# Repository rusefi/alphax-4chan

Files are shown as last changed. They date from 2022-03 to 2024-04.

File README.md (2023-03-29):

# AlphaX 4 channel

[buy at https://www.alphaxpr.com/](https://alphaxpr.com/product/4chan-neo/)

powerted by [rusEFI](https://github.com/rusefi/rusefi)

48 pin / 4 channel ECU

[User Documentation](https://github.com/rusefi/rusefi/wiki/AlphaX-4chan)

[Internal Documentation](https://docs.google.com/spreadsheets/d/1eW7kSP680lBT2MWl0ovFSy7t3at6WnlU7vX5ZDYfQZM)

Designed using [KiCAD 7](https://www.kicad.org/). Powered by [Hellen One](https://github.com/andreika-git/hellen-one) and [rusEFI](https://github.com/rusefi/rusefi)

Larger sibling of [alphax-2chan](https://github.com/rusefi/alphax-2chan)
Smaller sibling of [alphax-8chan](https://github.com/rusefi/alphax-8chan)

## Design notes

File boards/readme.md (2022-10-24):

4 layers

97 x 115 mm

1 Set 24 Pin FCI Ecu Oil To Gas Computer Board Connector Auto Housing Sealed Plug Socket 211PC249S8005 HCCPHPE24BKA90F

24Pin Auto FCI Oil To Gas Computer Board ECU Plug Electronic Connector Wiring Harness With 16/18AWG Cable

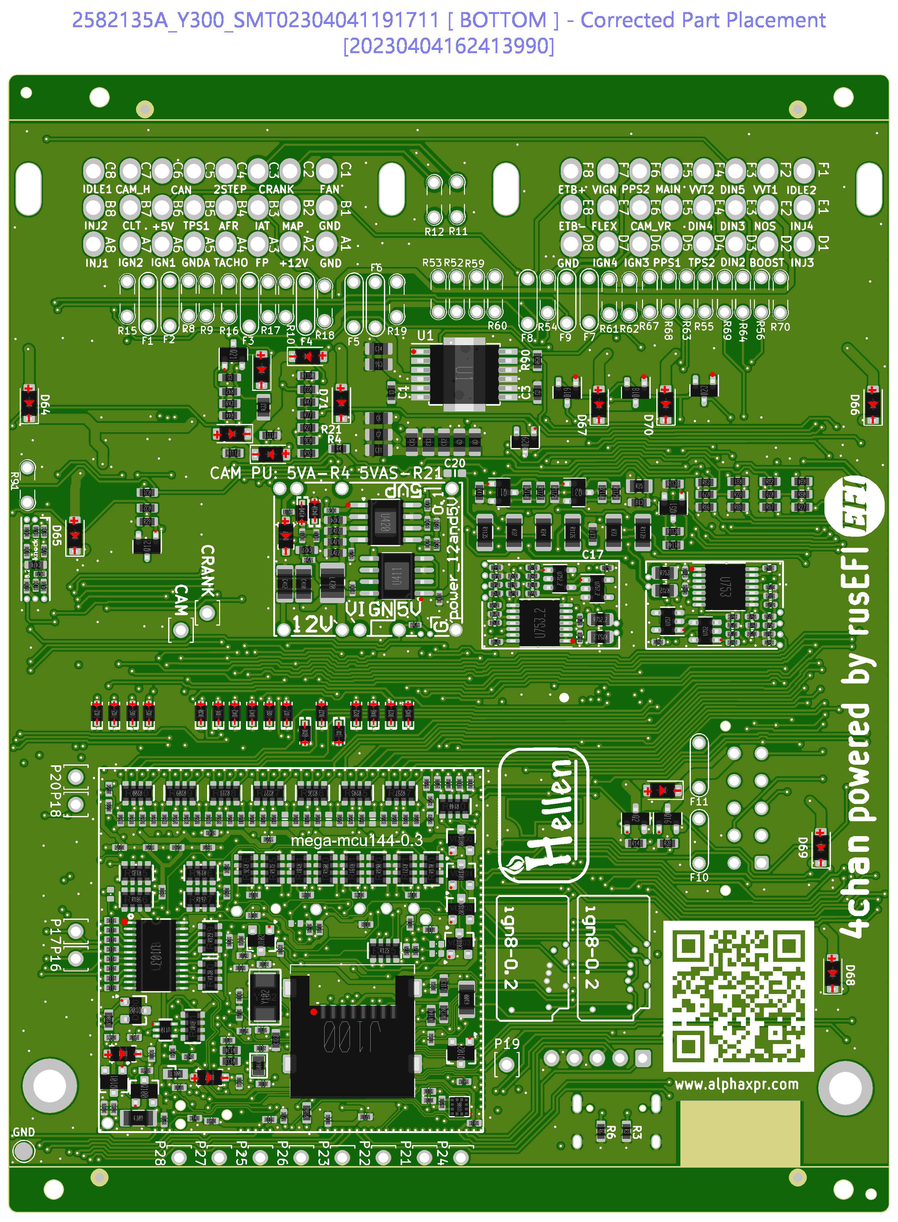
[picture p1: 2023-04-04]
boards/alphax_4ch-g/board/Produce_DanZhi.SMT_Snapshot.Bottom.2582135A_Y300.SMT02304041191711.png

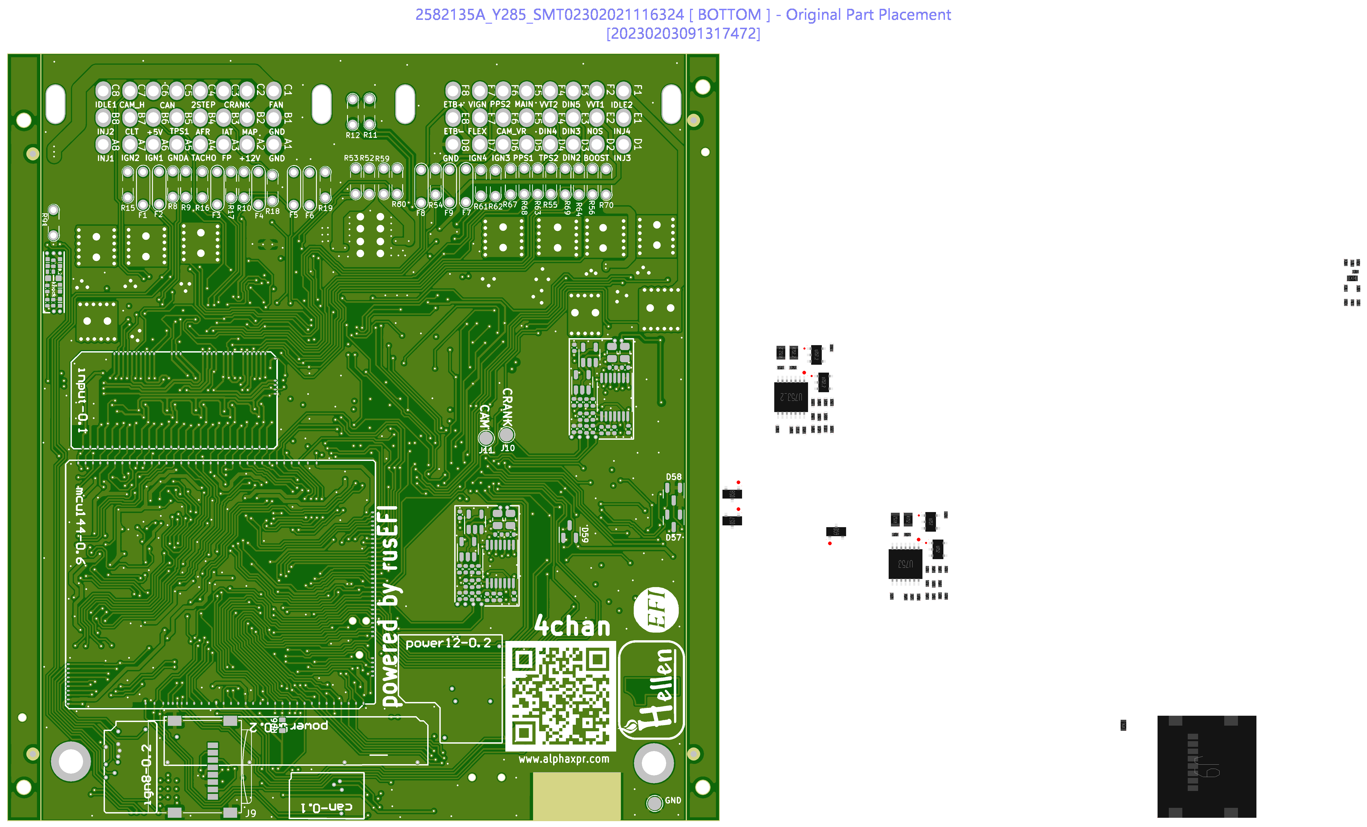
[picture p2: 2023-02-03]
boards/alphax_4ch-f.230202/board/Produce_DanZhi.SMT_Original_Snapshot.Bottom.2582135A_Y285.SMT02302021116324.png

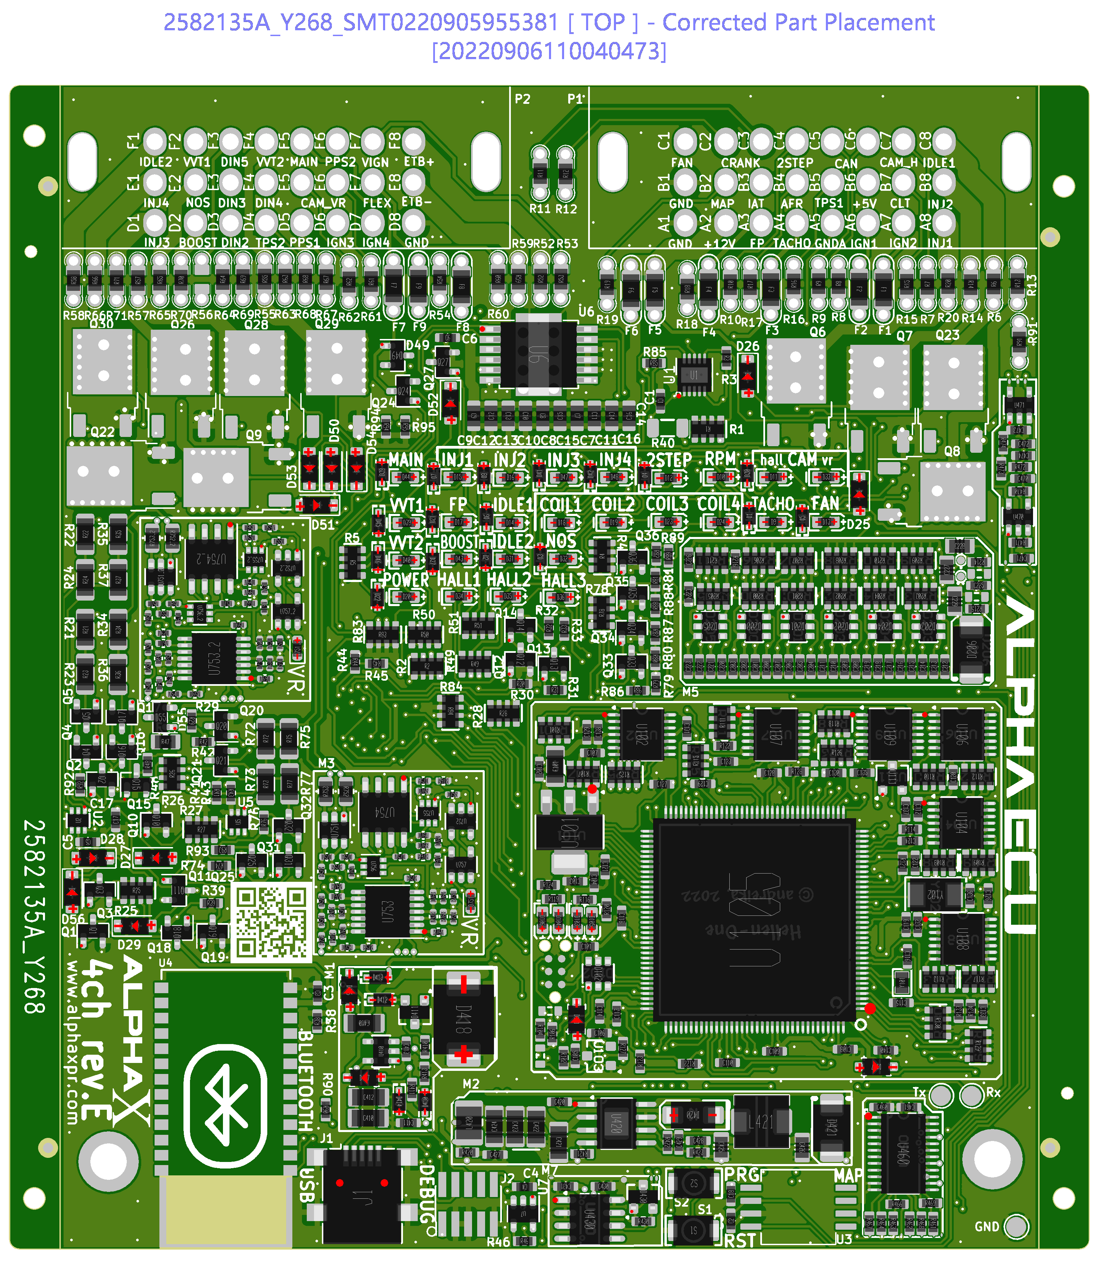
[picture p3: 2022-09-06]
boards/alphax_4ch-e.220905/board/Produce_DanZhi.SMT_Snapshot.Top.2582135A_Y268.SMT0220905955381.png

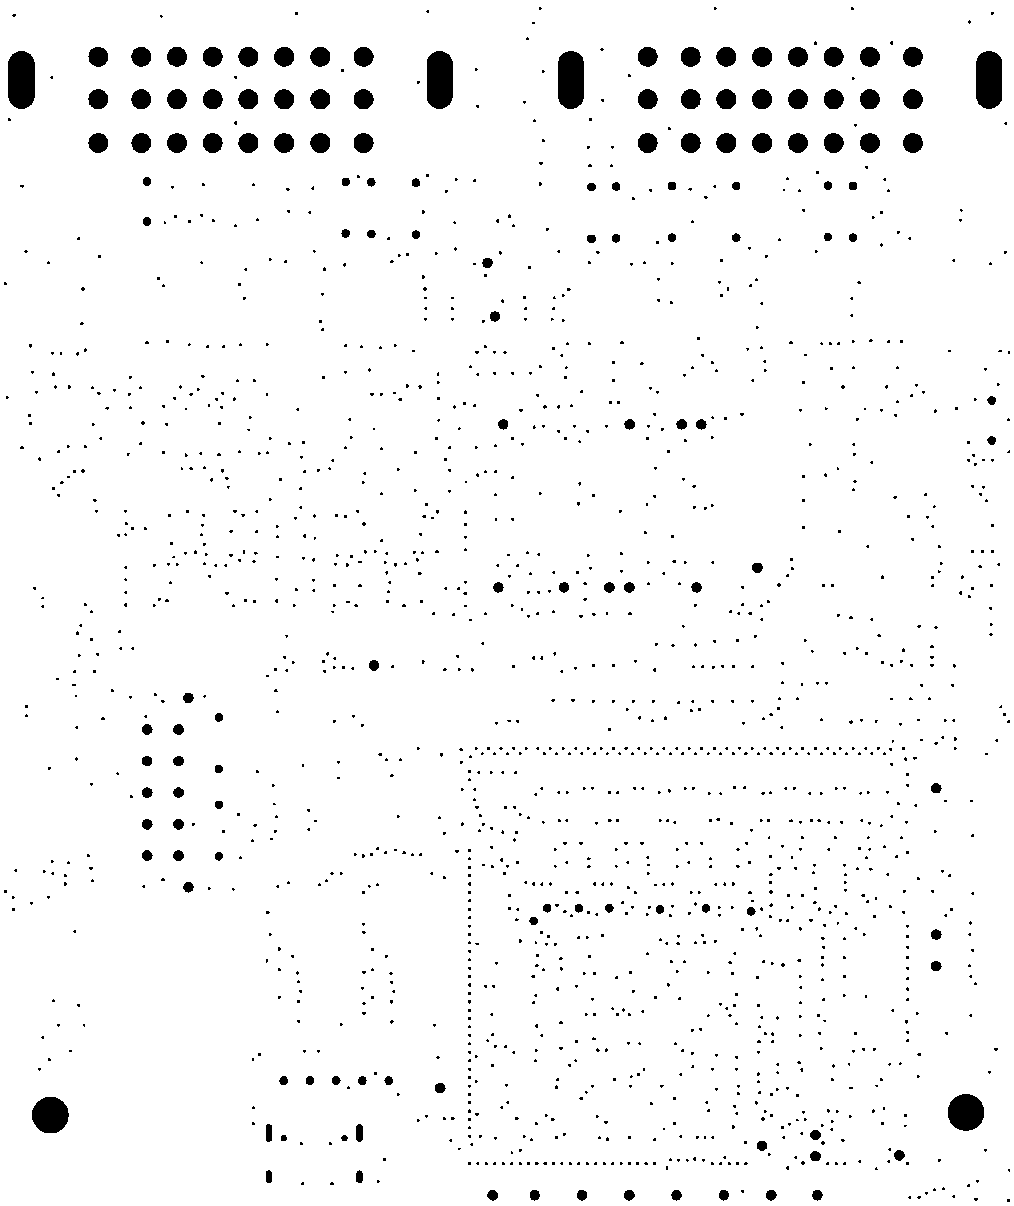
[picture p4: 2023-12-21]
boards/alphax_4ch-i/board/misc/alphax_4ch-i-outline.png

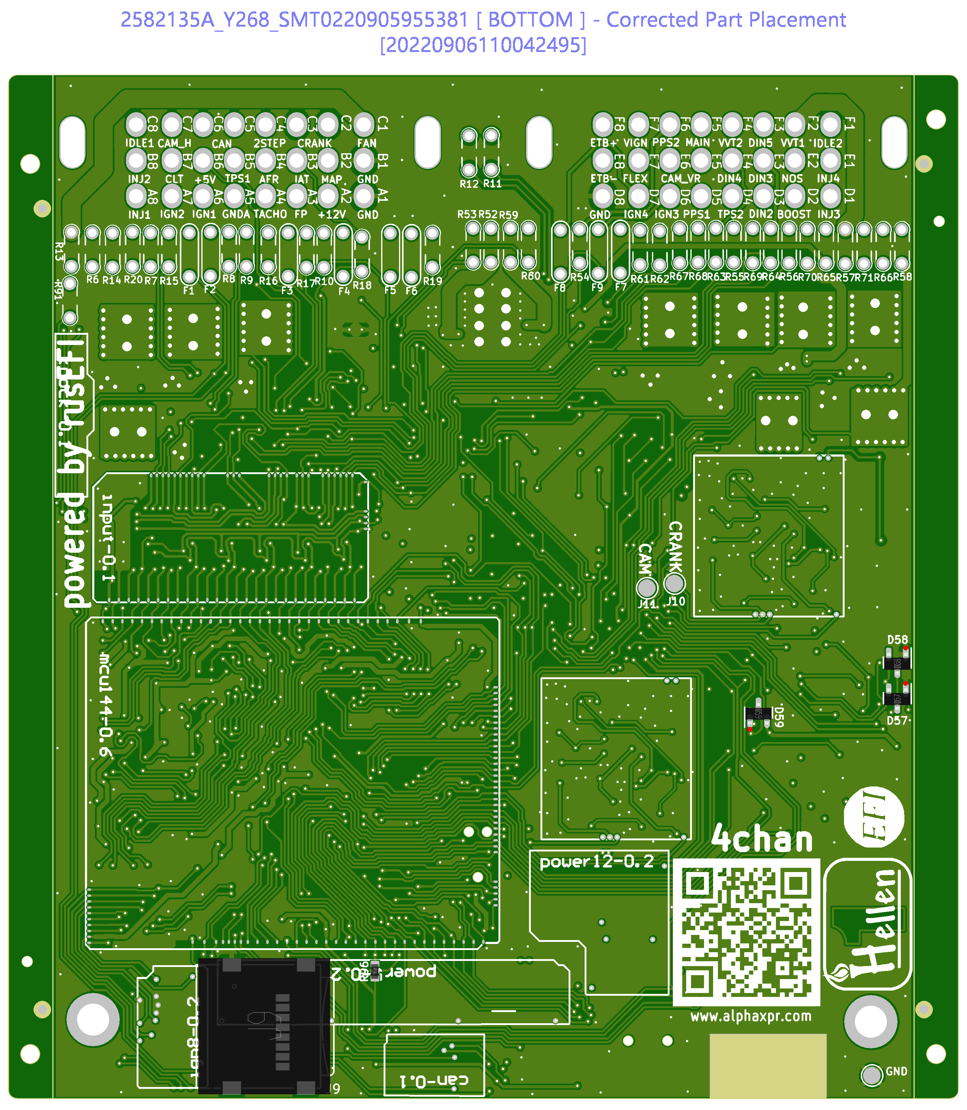
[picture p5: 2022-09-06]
boards/alphax_4ch-e.220905/board/Produce_DanZhi.SMT_Snapshot.Bottom.2582135A_Y268.SMT0220905955381.png

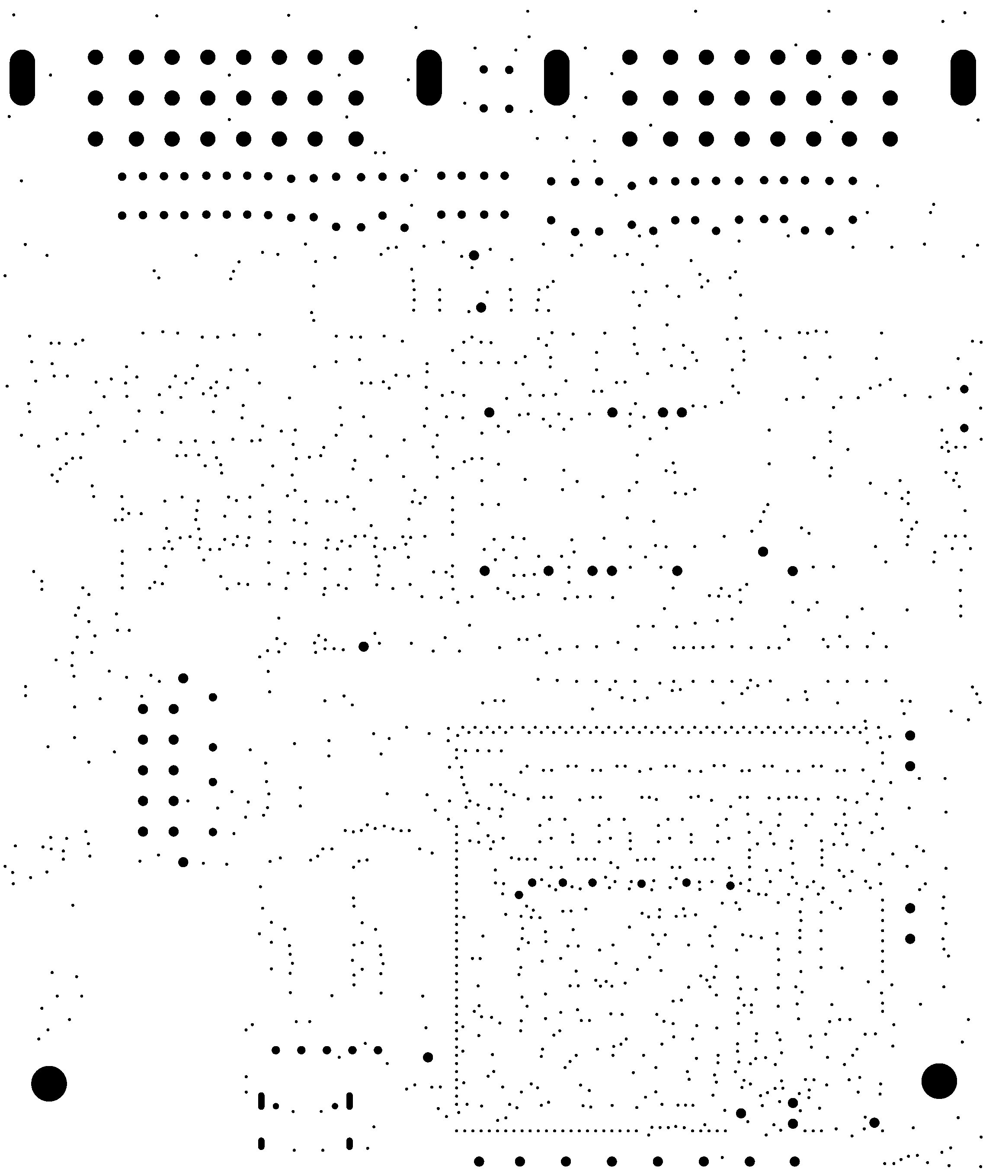
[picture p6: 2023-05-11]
boards/alphax_4ch-h.original/board/misc/alphax_4ch-h-outline.png

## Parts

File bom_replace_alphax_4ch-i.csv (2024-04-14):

############# MM SETUP ###############
# remove +5V pull-ups from SPI1, because we use it with +3.3v accelerometer
R103,
R105,
# remove jumper resistor connecting BOOT1 with A22 input line, because we use STM32F4
R131,
#CAN WAKEUP (disable O2S input)
R143,
############# MM SETUP ###############
# 4chan now prefers F42x for extra RAM
#U105,"STM32F427","LQFP144","C117816"
# F7 is even better than F42x!
U105,"STM32F767","LQFP144","C91685"
# DC-DC Inductor
L421,"MWSA0503S-100MT","MWSA0503","C408412"
L420,"NLCV32T-2R2M-EF","L1210","C250227"
# smart MOSFETs
"Q6,Q7,Q26,Q30,Q41,Q42,Q43,Q44,Q45,Q46,Q47,Q48","VND14NV04TR-E","DPAK","C2649436"
#MAX9142
"U754,U754_2","TLV3202AIDR","SO8","C129325"
#SD Card
J100,"TF-014-H16","SMD","C2874208"
# fuses
F410,"nSMD050-24V","SMD1206","C70076"
"F5,F6","Fuse-5A-1206","SMD1206","C553924"
"F1,F2,F8,F9,F10,F11","nSMD005","PAD-1206-PAD","C70064"
# TLS115
U411,"TLS115B0EJXUMA1","PG-DSO-8","C3743696"
# JLC shortage
R49,"4D03WGF1001T5E","R0603-4","C425239"
#20MHz crystal
Y102,"TXM20M0002503LFBEO00T","SMD5032-2P","C362485"
#WakeUP buffer
U110,"74LVC1G06SE-7","SOT-353","C460519"
#Blue LEDs
"D105,D109,D110,D111,D112,D113,D114,D115,D116","HL-PST-1608H203BC","LED0603","C497940"
#Green LEDs
"D20,D751,D104,D108,D751_2","XL-1608UGC-04","LED0603","C965804"
# remove R40 because we'll populate TLS115
R40,
#board ID capacitor shortage
C133,"1u","C0603","C519559"
# no software for accelerometer
U106,
#aux connector
J6,"430451012","02x05","C277725"
#mux
"U755,U756,U270,U275,U280,U285,U755_2,U756_2","WAS3157B-6","SOT-363","C213161"
# no Cortex 5x2 header
J2,"Cortex_Debug","PinHeader_2x05_P1.27mm_Vertical_SMD",""
# with MAP sensor
U3,"MPXH6400A","MPXH6400A-SSOP8","C511770"
# shortage
"R49","4D03WGF1001T5E","R0603-4","C110021"
#D1-D4 0 series
R140,"0","R0603x4","C1952"
# black main connector
P1,"HCCPHPE24BKA90F","33311-24AW-2","C5349068"
#include hellen-one/board_id/generated/board_id_alpha4ch-i.csv
#include bom_pullups_alphax_4ch-i.csv

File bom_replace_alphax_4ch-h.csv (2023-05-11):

############# MM SETUP ###############
# remove +5V pull-ups from SPI1, because we use it with +3.3v accelerometer
R103,
R105,
# remove jumper resistor connecting BOOT1 with A22 input line, because we use STM32F4
R131,
#CAN WAKEUP (disable O2S input)
R143,
############# MM SETUP ###############
# 4chan now prefers F42x for extra RAM
U105,"STM32F427","LQFP144","C117816"
# DC-DC Inductor
L421,"MWSA0503S-100MT","MWSA0503","C408412"
# smart MOSFETs
"Q6,Q7,Q26,Q30,Q41,Q42,Q43,Q44,Q45,Q46,Q47,Q48","VND10N06TR-E","DPAK","C2149912"
#SD Card
J100,"TF-014-H16","SMD","C2874208"
# fuses
F410,"nSMD050-24V","SMD1206","C70076"
"F5,F6","Fuse-5A-1206","SMD1206","C553924"
"F1,F2,F8,F9,F10,F11","nSMD005","PAD-1206-PAD","C70064"
# TLS115
U411,"TLS115B0EJXUMA1","PG-DSO-8","C3743696"
# JLC shortage
R49,"4D03WGF1001T5E","R0603-4","C425239"
#20MHz crystal
Y102,"TXM20M0002503LFBEO00T","SMD5032-2P","C362485"
#SMCJ30A
D418,"SMCJ30A","SMC","C320561"
#WakeUP buffer
U110,"74LVC1G06SE-7","SOT-353","C460519"
# remove R40 because we'll populate TLS115
R40,
# no software for accelerometer
U1001,
# no Cortex 5x2 header
J2,"Cortex_Debug","PinHeader_2x05_P1.27mm_Vertical_SMD",""
# no MAP sensor
U3,"MPXH6400A","MPXH6400A-SSOP8",""
#D1-D4 0 series
R140,"0","R0603x4","C1952"
#include hellen-one/board_id/generated/board_id_alpha4ch-h.csv
#include bom_pullups_alphax_4ch-h.csv

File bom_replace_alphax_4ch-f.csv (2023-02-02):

# remove the jumper connection from VCC_PP1 to +5V: we need +12v power supply for push-pull outputs.
R309
# remove +5V pull-ups from SPI1 | because we use it with +3.3v accelerometer
R103
R105
# remove jumper resistor connecting BOOT1 with A22 input line | because we use STM32F4
R131
# STM32
U105 | STM32F407ZGT6 | LQFP144 | C19156
#Alpha4Ch: We don't use VREF1 & VREF2 | so we don't need these resistors
R212
R213
# DC-DC Inductor
L421 | MWSA0503S-100MT | MWSA0503 | C408412
L420 | LBC3225T2R2MR | L1210 | C223413
# LMR14020->LMR14030 (more power | no problem)
U420 | LMR14030 | SOP8 | C182078
#fuses
F101 | nSMD035-16V | SMD1206 | C70072
F410 | nSMD050-24V | SMD1206 | C70076
F300 | nSMD050-24V | SMD1206 | C70076
F5 | Fuse-5A-1206 | SMD1206 | C553924
F6 | Fuse-5A-1206 | SMD1206 | C553924
#power distribution
U103 | AP2331W-7 | SOT-23 | C460346
U480 | AP2331W-7 | SOT-23 | C460346
# JLC-BOM stock shortages...
U420 | LMR14020SDDAR | SOP8 | C187824
S1 | TS-1088R-02026 | SMD-2_2.9x3.9x1.7 | C455280
S2 | TS-1088R-02026 | SMD-2_2.9x3.9x1.7 | C455280
L420 | NLV32T-2R2J-PF | L1210 | C89016
R4,R49 | 4D03WGF1001T5E | R0603-4 | C425239
# trigger schmidt buffer
U2,U5 | 74LVC2G17GW | SOT-363 | C80500
# analog switches for VR-discrete
U755, U756, U755_2, U756_2 | WAS3157B-6 | SOT-363 | C213161
U754, U754_2 | TLV3202AIDR | SO8 | C129325
# smart MOSFETs
Q6 | VND10N06TR-E | DPAK | C2149912
Q7 | VND10N06TR-E | DPAK | C2149912
Q8 | VND10N06TR-E | DPAK | C2149912
Q9 | VND10N06TR-E | DPAK | C2149912
Q22 | VND10N06TR-E | DPAK | C2149912
Q23 | VND10N06TR-E | DPAK | C2149912
Q26 | VND10N06TR-E | DPAK | C2149912
Q28 | VND10N06TR-E | DPAK | C2149912
Q29 | VND10N06TR-E | DPAK | C2149912
Q30 | VND10N06TR-E | DPAK | C2149912
# no TLE9201SG
U6 | IFX9201SG | Infineon_PG-DSO-12-11 | C112633
# use cheaper components
Q1, Q2, Q10, Q11, Q12, Q15, Q19, Q20, Q21, Q24, Q25, Q27, Q33, Q34, Q35, Q36 | AO3400A | SOT-23 | C700953
Q3, Q4, Q5, Q13, Q14, Q16, Q17, Q18, Q31, Q32 | AO3401A | SOT-23 | C700954
#
U752, U757, U752_2, U757_2 | 74AHC1G02 | SOT23-5 | C163710
F1, F2, F8, F9 | nSMD005 | PAD-1206-PAD | C70064
#a bit optional
U103
# remove R40 because we'll populate TLS115
R40
# no Cortex 5x2 header
J2 | Cortex_Debug | PinHeader_2x05_P1.27mm_Vertical_SMD
# no MAP sensor
U3 | MPXH6400A | MPXH6400A-SSOP8
#include hellen-one/board_id/generated/board_id_alpha4ch-f.csv

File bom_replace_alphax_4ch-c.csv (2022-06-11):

# remove the jumper connection from VCC_PP1 to +5V: we need +12v power supply for push-pull outputs.
R309
# remove +5V pull-ups from SPI1 | because we use it with +3.3v accelerometer
R103
R105
# remove jumper resistor connecting BOOT1 with A22 input line | because we use STM32F4
R131
# STM32
U105 | STM32F407ZGT6 | LQFP144 | C19156
#Alpha4Ch: We don't use VREF1 & VREF2 | so we don't need these resistors
R212
R213
# DC-DC Inductor
L421 | MWSA0503S-100MT | MWSA0503 | C408412
L420 | LBC3225T2R2MR | L1210 | C223413
# LMR14020->LMR14030 (more power | no problem)
U420 | LMR14030 | SOP8 | C182078
#fuses
F101 | nSMD035-16V | SMD1206 | C70072
F410 | nSMD050-24V | SMD1206 | C70076
F300 | nSMD050-24V | SMD1206 | C70076
F5 | Fuse-5A-1206 | SMD1206 | C553924
F6 | Fuse-5A-1206 | SMD1206 | C553924
#power distribution
U103 | AP2331W-7 | SOT-23 | C460346
U480 | AP2331W-7 | SOT-23 | C460346
# JLC-BOM stock shortages...
U420 | LMR14020SDDAR | SOP8 | C187824
S1 | TS-1088R-02026 | SMD-2_2.9x3.9x1.7 | C455280
S2 | TS-1088R-02026 | SMD-2_2.9x3.9x1.7 | C455280
L420 | NLV32T-2R2J-PF | L1210 | C89016
R4 | 4D03WGF1001T5E | R0603-4 | C425239
# trigger schmidt buffer
U2 | 74HC2G17GW | SOT-363 | C94189
U5 | 74HC2G17GW | SOT-363 | C94189
# analog switches for VR-discrete
U755, U756, U755_2, U756_2 | WAS3157B-6 | SOT-363 | C213161
# smart MOSFETs
Q6 | VND14NV04TR-E | DPAK | C2649436
Q7 | VND14NV04TR-E | DPAK | C2649436
Q8 | VND14NV04TR-E | DPAK | C2649436
Q9 | VND14NV04TR-E | DPAK | C2649436
Q22 | VND14NV04TR-E | DPAK | C2649436
Q23 | VND14NV04TR-E | DPAK | C2649436
Q26 | VND14NV04TR-E | DPAK | C2649436
Q28 | VND14NV04TR-E | DPAK | C2649436
Q29 | VND14NV04TR-E | DPAK | C2649436
Q30 | VND14NV04TR-E | DPAK | C2649436
# use cheaper components
Q1, Q2, Q10, Q11, Q12, Q15, Q19, Q20, Q21, Q24, Q25, Q27, Q33, Q34, Q35, Q36 | AO3400A | SOT-23 | C700953
Q3, Q4, Q5, Q13, Q14, Q16, Q17, Q18, Q31, Q32 | AO3401A | SOT-23 | C700954
# remove R40 because we'll populate TLS115
R40
# no TLS115
U1 | TLS115 | PG-DSO-8-43
# no Cortex 5x2 header
J2 | Cortex_Debug | PinHeader_2x05_P1.27mm_Vertical_SMD
# no MAP sensor
U3 | MPXH6400A | MPXH6400A-SSOP8
# no TLE9201SG
U6 | TLE9201SG | Infineon_PG-DSO-12-11
#include board_id_alpha4ch-c.csv

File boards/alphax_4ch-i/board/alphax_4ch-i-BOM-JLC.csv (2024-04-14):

Comment | Designator | Footprint | LCSC Part #
10n | C1, C3 | C0603 | C57112
100n | C2, C5, C6, C18, C19, C55, C460, C461, C460_2, C461_2 | C0603 | C14663
1n | C4 | C0603 | C1588
22u | C7, C117, C123 | C0603 | C59461
1n 250V | C8, C9, C17, C20, C21 | C0603 | C277510
10u | C45, C46, C47, C48, C49, C50, C51, C52, C53, C54 | C0805 | C15850
1N4148WS | D1, D2, D3, D5, D6, D7, D8, D21, D22, D24, D37, D38, D41, D42, D45, D46, D53, D410, D412, D413, D414 | SOD-323 | C2128
LED-WHITE-0603 | D4, D10, D33, D34, D35, D36 | LED-0603 | C2290
LED-RED-0603 | D9, D13, D14, D15, D16, D17, D31, D32, D39, D40, D43, D44, D47, D48, D56, D57, D103 | LED-0603 | C2286
BAT54S | D18, D19, D23, D55, D58, VD100, VD101, VD102, VD103 | SOT-23 | C47546
PSM712-LF | D25, D28, D29, D411 | SOT-23 | C32677
B5819W | D26, D27, D49, D50, D51, D52, D64, D65, D66, D67, D68, D69, D70, D71, D72, D416, D417, D101, D107 | SOD-123 | C8598
nSMD050 | F3, F4, F7 | PAD-1206-PAD | C720075
USB_C_Receptacle_USB2.0 | J1 | USB_C_Receptacle_XKB_U262-16XN-4BVC11 | C2927038
AO3400A | Q1, Q3, Q4, Q8, Q9, Q10, Q11, Q12, Q17, Q20, Q22, Q23, Q24, Q27, Q29, Q31, Q51, Q101, Q103 | SOT-23 | C20917
PJM2319PSA | Q2, Q16 | SOT-23 | C411720
AO3401A | Q13, Q14, Q18, Q19, Q21, Q25, Q28, Q35, Q36, Q49, Q50, Q52, Q53, Q100, Q102 | SOT-23 | C15127
4.7k | R1, R2, R5, R26, R50, R51, R125, R170, R171, R175, R176, R180, R181, R185, R186, R190, R191, R196, R197, R200, R209, R218, R227, R236, R245, R257 | R0603-4 | C66697
5.6k | R3, R6 | R0603 | C23189
2k | R4, R18, R19, R34, R1126, R1131, R1135, R1136, R1139, R1141 | R1206 | C17944
4.7k | R7, R8, R14, R20, R27, R29, R30, R38, R39, R41, R42, R43, R44, R52, R53, R54, R55, R57, R86, R87, R88, R98, R99, R1100, R1101, R1102, R1103, R1104, R1105, R1106, R1107, R1108, R1109, R1110, R1111, R1112, R1113, R1125, R1127, R1128, R1129, R1132, R1137, R1138, R1140 | R0603 | C23162
4.7k | R9, R10, R11, R12, R21, R22, R23, R24, R35, R36, R37, R47, R72, R73 | R1206 | C17936
10k | R16 | R0603 | C25804
33k | R17, R120 | R0603 | C4216
470 | R25 | R0805 | C17710
1.2k | R28, R78, R79, R80 | R0603 | C22765
2.7k | R31, R32 | R0603 | C13167
220 | R33 | R0805 | C17557
SMD1206B035TF/16 | F100, F101 | R1206 | C269114
750 | R45 | R0805 | C17818
680k | R46, R74, R76, R93 | R0603 | C25822
Jumper-Pad-Pad | R56, R91 | PAD-0805-PAD | C17477
6.8k | R58 | R0603 | C23212
3.3k | R81, R82, R83, R84, R85 | R0603 | C22978
MAX9924UAUB+ | U1 | MSOP-10_3x3mm_P0.5mm | C143633
TLE9201SG | U7 | Infineon_PG-DSO-12-11 | C112633
47u | C410, C412 | C1206 | C96123
100n | C411, C413, C420, C470, C203, C202, C207, C206, C205, C204, C217, C218, C225, C226 | C0402 | C307331
1u | C414, C415, C755, C758, C761, C762, C763, C765, C766, C767, C755_2, C758_2, C761_2, C762_2, C763_2, C765_2, C766_2, C767_2 | C0402 | C52923
10u | C421, C422, C423, C424, C425, C426 | C0603 | C96446
4.7u | C427 | C0603 | C19666
10n | C428, C756, C757, C760, C764, C768, C769, C756_2, C757_2, C760_2, C764_2, C768_2, C769_2, C213, C214 | C0402 | C15195
220p | C429 | C0402 | C1530
SMCJ30A | D418 | SMC | C310046
SS34 | D420 | SMA | C8678
P6SMB6.8CA | D421, D205 | SMB | C78395
MHT136UGCT | LED1, LED2, LED3, LED4 | LED0402 | C434447
6.8k | R410, R413 | R0402 | C25917
33k | R411, R424, R425, R474 | R0402 | C25779
1 | R420 | R0402 | C25086
10k | R421, R426, R427, R757, R762, R763, R767, R768, R102, R107, R108, R109, R121, R127, R128, R141, R142, R757_2, R762_2, R763_2, R767_2, R768_2, R233, R234 | R0402 | C25744
68k | R422, R760, R760_2 | R0402 | C36871
12k | R423, R754, R754_2, R472 | R0402 | C25752
4.7k | R428, R144, R210 | R0402 | C25900
MIC5205-3.3YM5 | U410 | SOT23-5 | C37970
LMR14020 | U420 | SOP8 | C187824
10 | R461, R462, R463, R464, R466, R467, R468, R469, R461_2, R462_2, R463_2, R464_2, R466_2, R467_2, R468_2, R469_2 | R0603 | C22859
SN74LVC4245APWR | U460, U103, U460_2 | TSSOP24 | C7859
1n | C751, C135, C139, C141, C142, C751_2, C211, C209, C208, C201, C200, C216, C219, C215, C212, C227, C230, C231, C232, C233, C210, C143, C144, C145, C146 | C0402 | C1523
470n | C752, C752_2 | C0402 | C47339
100n | C753, C754, C759, C100, C101, C105, C108, C109, C110, C111, C112, C113, C118, C119, C120, C121, C122, C124, C126, C127, C128, C129, C130, C134, C147, C170, C175, C180, C185, C190, C195, C220, C221, C222, C270, C275, C280, C285, C753_2, C754_2, C759_2 | C0402 | C1525
2.2k | R751, R122, R123, R146, R147, R751_2 | R0402 | C25879
10k | R752, R753, R752_2, R753_2 | R0805 | C17414
100k | R755, R756, R758, R759, R755_2, R756_2, R758_2, R759_2, R471, R473 | R0402 | C25741
10 | R761, R764, R769, R110, R111, R112, R113, R114, R115, R116, R117, R761_2, R764_2, R769_2 | R0402 | C25077
1k | R765, R766, R765_2, R766_2 | R0402 | C11702
SRV05-4-P-T7 | U751, D102, D200, D201, D202, D203, D204, D206, D207, U751_2 | SOT23-6 | C85364
74AHC1G02 | U752, U757, U752_2, U757_2 | SOT23-5 | C7463
MCP6004 | U753, U170, U175, U180, U185, U190, U195, U753_2 | TSSOP14 | C50282
TJA1051T/3/1J | U100 | SO8 | C38695
REF3033 | U102 | SOT-23 | C36658
PESD1CAN | D100 | SOT-23 | C343993
LPS22HBTR | U107 | HLGA-10L | C94049
LED-YELLOW-0603 | D106 | LED-0603 | C72038
LDL1117S33R | U101 | SOT-223 | C435835
BTN | S100, S101 | SMD-2_2.9x3.9x1.7 | C115357
BLM18AG601SN1D | L100 | L0603 | C19330
680k | R222, R208, R207, R242, R243, R237, R250, R251, R225 | R0402 | C163456
510 | R254, R255, R256, R258 | R0402 | C25123
470 | R101, R118, R119 | R0603-4 | C25510
120 | R100 | R0603 | C22787
100 | R104, R106 | R0603 | C22775
74LVC2G17GW,125 | U108, U109 | SOT-363 | C80500
32.768 kHz | Y101 | SMD2012 | C99009
18p | C132, C136 | C0402 | C1549
12p | C115, C116 | C0402 | C1547
10k | R129, R130 | R0603-4 | C29718
5.1k | R195 | R0402 | C25905
4.7u | C102, C103, C104, C106, C107, C137, C138, C140 | C0402 | C23733
2.2u | C114, C131, C223, C224, C229 | C0402 | C12530
0 | R145 | R0402 | C17168
3.3n | C471 | C0402 | C26404
330p | C472 | C0402 | C13533
47p | C473 | C0402 | C1567
680p | C474 | C0603 | C1630
470k | R470 | R0402 | C25790
LMV321IDBVR | U470, U471 | SOT23-5 | C7972
STM32F767 | U105 | LQFP144 | C91685
MWSA0503S-100MT | L421 | MWSA0503 | C408412
NLCV32T-2R2M-EF | L420 | L1210 | C250227
VND14NV04TR-E | Q6, Q7, Q26, Q30, Q41, Q42, Q43, Q44, Q45, Q46, Q47, Q48 | DPAK | C2649436
TLV3202AIDR | U754, U754_2 | SO8 | C129325
TF-014-H16 | J100 | SMD | C2874208
nSMD050-24V | F410 | SMD1206 | C70076
Fuse-5A-1206 | F5, F6 | SMD1206 | C553924
nSMD005 | F1, F2, F8, F9, F10, F11 | PAD-1206-PAD | C70064
TLS115B0EJXUMA1 | U411 | PG-DSO-8 | C3743696
TXM20M0002503LFBEO00T | Y102 | SMD5032-2P | C362485
74LVC1G06SE-7 | U110 | SOT-353 | C460519
HL-PST-1608H203BC | D105, D109, D110, D111, D112, D113, D114, D115, D116 | LED0603 | C497940
XL-1608UGC-04 | D20, D751, D104, D108, D751_2 | LED0603 | C965804
1u | C133 | C0603 | C519559
430451012 | J6 | 02x05 | C277725
WAS3157B-6 | U755, U756, U270, U275, U280, U285, U755_2, U756_2 | SOT-363 | C213161
MPXH6400A | U3 | MPXH6400A-SSOP8 | C511770
4D03WGF1001T5E | R49 | R0603-4 | C110021
0 | R140 | R0603x4 | C1952
HCCPHPE24BKA90F | P1 | 33311-24AW-2 | C5349068
750 | R133 | R0603 | C23241
1500 | R134 | R0603 | C22843

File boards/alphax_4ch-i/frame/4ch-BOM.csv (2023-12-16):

Comment | Designator | Footprint | LCSC Part #
10n | C1 | C0603 | C57112
100n | C2 | C0603 | C14663
10n | C3 | C0603 | C57112
1n | C4 | C0603 | C1588
100n | C5 | C0603 | C14663
100n | C6 | C0603 | C14663
22u | C7 | C0603 | C59461
1n 250V | C8 | C0603 | C277510
1n 250V | C9 | C0603 | C277510
1n 250V | C17 | C0603 | C277510
100n | C18 | C0603 | C14663
100n | C19 | C0603 | C14663
1n 250V | C20 | C0603 | C277510
1n 250V | C21 | C0603 | C277510
470uF | C22 | CP_Elec_10x10.5
10u | C45 | C0805 | C15850
10u | C46 | C0805 | C15850
10u | C47 | C0805 | C15850
10u | C48 | C0805 | C15850
10u | C49 | C0805 | C15850
10u | C50 | C0805 | C15850
10u | C51 | C0805 | C15850
10u | C52 | C0805 | C15850
10u | C53 | C0805 | C15850
10u | C54 | C0805 | C15850
100n | C55 | C0603 | C14663
1N4148WS | D1 | SOD-323 | C2128
1N4148WS | D2 | SOD-323 | C2128
1N4148WS | D3 | SOD-323 | C2128
LED-WHITE-0603 | D4 | LED-0603 | C2290
1N4148WS | D5 | SOD-323 | C2128
1N4148WS | D6 | SOD-323 | C2128
1N4148WS | D7 | SOD-323 | C2128
1N4148WS | D8 | SOD-323 | C2128
LED-RED-0603 | D9 | LED-0603 | C2286
LED-WHITE-0603 | D10 | LED-0603 | C2290
LED-RED-0603 | D13 | LED-0603 | C2286
LED-RED-0603 | D14 | LED-0603 | C2286
LED-RED-0603 | D15 | LED-0603 | C2286
LED-RED-0603 | D16 | LED-0603 | C2286
LED-RED-0603 | D17 | LED-0603 | C2286
BAT54S | D18 | SOT-23 | C47546
BAT54S | D19 | SOT-23 | C47546
LED-GREEN-0603 | D20 | LED-0603 | C72043
1N4148WS | D21 | SOD-323 | C2128
1N4148WS | D22 | SOD-323 | C2128
BAT54S | D23 | SOT-23 | C47546
1N4148WS | D24 | SOD-323 | C2128
PSM712-LF | D25 | SOT-23 | C32677
B5819W | D26 | SOD-123 | C8598
B5819W | D27 | SOD-123 | C8598
PSM712-LF | D28 | SOT-23 | C32677
PSM712-LF | D29 | SOT-23 | C32677
LED-RED-0603 | D31 | LED-0603 | C2286
LED-RED-0603 | D32 | LED-0603 | C2286
LED-WHITE-0603 | D33 | LED-0603 | C2290
LED-WHITE-0603 | D34 | LED-0603 | C2290
LED-WHITE-0603 | D35 | LED-0603 | C2290
LED-WHITE-0603 | D36 | LED-0603 | C2290
1N4148WS | D37 | SOD-323 | C2128
1N4148WS | D38 | SOD-323 | C2128
LED-RED-0603 | D39 | LED-0603 | C2286
LED-RED-0603 | D40 | LED-0603 | C2286
1N4148WS | D41 | SOD-323 | C2128
1N4148WS | D42 | SOD-323 | C2128
LED-RED-0603 | D43 | LED-0603 | C2286
LED-RED-0603 | D44 | LED-0603 | C2286
1N4148WS | D45 | SOD-323 | C2128
1N4148WS | D46 | SOD-323 | C2128
LED-RED-0603 | D47 | LED-0603 | C2286
LED-RED-0603 | D48 | LED-0603 | C2286
B5819W | D49 | SOD-123 | C8598
B5819W | D50 | SOD-123 | C8598
B5819W | D51 | SOD-123 | C8598
B5819W | D52 | SOD-123 | C8598
1N4148WS | D53 | SOD-323 | C2128
BAT54S | D55 | SOT-23 | C47546
LED-RED-0603 | D56 | LED-0603 | C2286
LED-RED-0603 | D57 | LED-0603 | C2286
BAT54S | D58 | SOT-23 | C47546
B5819W | D64 | SOD-123 | C8598
B5819W | D65 | SOD-123 | C8598
B5819W | D66 | SOD-123 | C8598
B5819W | D67 | SOD-123 | C8598
B5819W | D68 | SOD-123 | C8598
B5819W | D69 | SOD-123 | C8598
B5819W | D70 | SOD-123 | C8598
B5819W | D71 | SOD-123 | C8598
B5819W | D72 | SOD-123 | C8598
nSMD005 | F1 | PAD-1206-PAD | C369153
nSMD005 | F2 | PAD-1206-PAD | C369153
nSMD050 | F3 | PAD-1206-PAD | C720075
nSMD050 | F4 | PAD-1206-PAD | C720075
12H1500D | F5 | PAD-1206-PAD | C182446
12H1500D | F6 | PAD-1206-PAD | C182446
nSMD050 | F7 | PAD-1206-PAD | C720075
nSMD005 | F8 | PAD-1206-PAD | C369153
nSMD005 | F9 | PAD-1206-PAD | C369153
nSMD005 | F10 | PAD-1206-PAD | C369153
nSMD005 | F11 | PAD-1206-PAD | C369153
RUSEFI_LOGO | G1 | rusefi_logo
LOGO | G3 | LOGO
LOGO_AlphaECU | G4 | alphax_logo_AlphaECU
LOGO_AlphaX | G5 | alphax_logo_AlphaX
ALPHAX_QR_CODE | G6 | alphax_qr_code
Disclaimer | G7 | Off_Road_Disclaimer
USB_C_Receptacle_USB2.0 | J1 | USB_C_Receptacle_XKB_U262-16XN-4BVC11 | C2927038
Cortex_Debug | J2 | PinHeader_2x05_P1.27mm_Vertical_SMD | C448647
Conn_01x01 | J3 | TestPoint_Pad_D2.0mm
Conn_01x01 | J4 | TestPoint_Pad_D2.0mm
Conn_01x05_Male | J5 | Molex_SPOX_5267-05A_1x05_P2.50mm_Vertical
430451012 | J6 | Molex_Micro-Fit_3.0_43045-1012_2x05_P3.00mm_Vertical | C239457
Conn_01x01 | J7 | MountingHole_4.5mm_Pad
Conn_01x01 | J8 | MountingHole_4.5mm_Pad
Module:power_12and5V/0.2 | M1 | power_12and5V
Module:ign8/0.2 | M2 | ign8
Module:vr-discrete/0.4 | M3 | vr-discrete
Module:mega-mcu144/0.5 | M4 | mega-mcu144
Module:ign8/0.2 | M6 | ign8
Module:vr-discrete/0.4 | M8 | vr-discrete
Module:knock/0.2 | M9 | knock
HCCPHPE24BKA90F | P1 | 33311-24AW-2
HCCPHPE24BGYB90F | P2 | 33311-24AW-2
Pad | P4 | PAD-TH
Pad | P16 | PAD-TH
Pad | P17 | PAD-TH
Pad | P18 | PAD-TH
Pad | P19 | PAD-TH
Pad | P21 | PAD-TH
Pad | P22 | PAD-TH
Pad | P23 | PAD-TH
Pad | P24 | PAD-TH
Pad | P25 | PAD-TH
Pad | P26 | PAD-TH
Pad | P27 | PAD-TH
Pad | P28 | PAD-TH
AO3400A | Q1 | SOT-23 | C20917
PJM2319PSA | Q2 | SOT-23 | C411720
AO3400A | Q3 | SOT-23 | C20917
AO3400A | Q4 | SOT-23 | C20917
VND14NV04-E | Q6 | DPAK | C155647
VND14NV04-E | Q7 | DPAK | C155647
AO3400A | Q8 | SOT-23 | C20917
AO3400A | Q9 | SOT-23 | C20917
AO3400A | Q10 | SOT-23 | C20917
AO3400A | Q11 | SOT-23 | C20917
AO3400A | Q12 | SOT-23 | C20917
AO3401A | Q13 | SOT-23 | C15127
AO3401A | Q14 | SOT-23 | C15127
PJM2319PSA | Q16 | SOT-23 | C411720
AO3400A | Q17 | SOT-23 | C20917
AO3401A | Q18 | SOT-23 | C15127
AO3401A | Q19 | SOT-23 | C15127
AO3400A | Q20 | SOT-23 | C20917
AO3401A | Q21 | SOT-23 | C15127
AO3400A | Q22 | SOT-23 | C20917
AO3400A | Q23 | SOT-23 | C20917
AO3400A | Q24 | SOT-23 | C20917
AO3401A | Q25 | SOT-23 | C15127
VND14NV04-E | Q26 | DPAK | C155647
AO3400A | Q27 | SOT-23 | C20917
AO3401A | Q28 | SOT-23 | C15127
AO3400A | Q29 | SOT-23 | C20917
VND14NV04-E | Q30 | DPAK | C155647
AO3400A | Q31 | SOT-23 | C20917
AO3401A | Q35 | SOT-23 | C15127
AO3401A | Q36 | SOT-23 | C15127
VND14NV04-E | Q41 | DPAK | C155647
VND14NV04-E | Q42 | DPAK | C155647
VND14NV04-E | Q43 | DPAK | C155647
VND14NV04-E | Q44 | DPAK | C155647
VND14NV04-E | Q45 | DPAK | C155647
VND14NV04-E | Q46 | DPAK | C155647
VND14NV04-E | Q47 | DPAK | C155647
VND14NV04-E | Q48 | DPAK | C155647
AO3401A | Q49 | SOT-23 | C15127
AO3401A | Q50 | SOT-23 | C15127
AO3400A | Q51 | SOT-23 | C20917
AO3401A | Q52 | SOT-23 | C15127
AO3401A | Q53 | SOT-23 | C15127
4.7k | R1 | R0603-4 | C66697
4.7k | R2 | R0603-4 | C66697
5.6k | R3 | R0603 | C23189
2k | R4 | R1206 | C17944
4.7k | R5 | R0603-4 | C66697
5.6k | R6 | R0603 | C23189
4.7k | R7 | R0603 | C23162
4.7k | R8 | R0603 | C23162
4.7k | R9 | R1206 | C17936
4.7k | R10 | R1206 | C17936
4.7k | R11 | R1206 | C17936
4.7k | R12 | R1206 | C17936
~ | R13 | R0603
4.7k | R14 | R0603 | C23162
~ | R15 | R0603
10k | R16 | R0603 | C25804
33k | R17 | R0603 | C4216
2k | R18 | R1206 | C17944
2k | R19 | R1206 | C17944
4.7k | R20 | R0603 | C23162
4.7k | R21 | R1206 | C17936
4.7k | R22 | R1206 | C17936
4.7k | R23 | R1206 | C17936
4.7k | R24 | R1206 | C17936
470 | R25 | R0805 | C17710
4.7k | R26 | R0603-4 | C66697
4.7k | R27 | R0603 | C23162
1.2k | R28 | R0603 | C22765
4.7k | R29 | R0603 | C23162
4.7k | R30 | R0603 | C23162
2.7k | R31 | R0603 | C13167
2.7k | R32 | R0603 | C13167
220 | R33 | R0805 | C17557
2k | R34 | R1206 | C17944
4.7k | R35 | R1206 | C17936
4.7k | R36 | R1206 | C17936
4.7k | R37 | R1206 | C17936
4.7k | R38 | R0603 | C23162
4.7k | R39 | R0603 | C23162
SMD1206B035TF/16 | R40 | R1206 | C269114
4.7k | R41 | R0603 | C23162
4.7k | R42 | R0603 | C23162
4.7k | R43 | R0603 | C23162
4.7k | R44 | R0603 | C23162
750 | R45 | R0805 | C17818
680k | R46 | R0603 | C25822
4.7k | R47 | R1206 | C17936
~ | R48 | R0603
1k | R49 | R0603-4 | C240722
4.7k | R50 | R0603-4 | C66697
4.7k | R51 | R0603-4 | C66697
4.7k | R52 | R0603 | C23162
4.7k | R53 | R0603 | C23162
4.7k | R54 | R0603 | C23162
4.7k | R55 | R0603 | C23162
Jumper-Pad-Pad | R56 | PAD-0805-PAD | C17477
4.7k | R57 | R0603 | C23162
6.8k | R58 | R0603 | C23212
4.7k | R72 | R1206 | C17936
4.7k | R73 | R1206 | C17936
680k | R74 | R0603 | C25822
~ | R75 | R0603
680k | R76 | R0603 | C25822
1.2k | R78 | R0603 | C22765
1.2k | R79 | R0603 | C22765
1.2k | R80 | R0603 | C22765
3.3k | R81 | R0603 | C22978
3.3k | R82 | R0603 | C22978
3.3k | R83 | R0603 | C22978
3.3k | R84 | R0603 | C22978
3.3k | R85 | R0603 | C22978
4.7k | R86 | R0603 | C23162
4.7k | R87 | R0603 | C23162
4.7k | R88 | R0603 | C23162
~ | R89 | R0603
Jumper-Pad-Pad | R91 | PAD-0805-PAD | C17477
680k | R93 | R0603 | C25822
4.7k | R98 | R0603 | C23162
4.7k | R99 | R0603 | C23162
4.7k | R1100 | R0603 | C23162
4.7k | R1101 | R0603 | C23162
4.7k | R1102 | R0603 | C23162
4.7k | R1103 | R0603 | C23162
4.7k | R1104 | R0603 | C23162
4.7k | R1105 | R0603 | C23162
4.7k | R1106 | R0603 | C23162
4.7k | R1107 | R0603 | C23162
4.7k | R1108 | R0603 | C23162
4.7k | R1109 | R0603 | C23162
4.7k | R1110 | R0603 | C23162
4.7k | R1111 | R0603 | C23162
4.7k | R1112 | R0603 | C23162
4.7k | R1113 | R0603 | C23162
4.7k | R1125 | R0603 | C23162
2k | R1126 | R1206 | C17944
4.7k | R1127 | R0603 | C23162
4.7k | R1128 | R0603 | C23162
4.7k | R1129 | R0603 | C23162
2k | R1131 | R1206 | C17944
4.7k | R1132 | R0603 | C23162
2k | R1135 | R1206 | C17944
2k | R1136 | R1206 | C17944
4.7k | R1137 | R0603 | C23162
4.7k | R1138 | R0603 | C23162
2k | R1139 | R1206 | C17944
4.7k | R1140 | R0603 | C23162
2k | R1141 | R1206 | C17944
MAX9924UAUB+ | U1 | MSOP-10_3x3mm_P0.5mm | C143633
MPXH6400A | U3 | MPXH6400A-SSOP8 | C511770
JDY-33 | U4 | JDY-33
TLE9201SG | U7 | Infineon_PG-DSO-12-11 | C112633

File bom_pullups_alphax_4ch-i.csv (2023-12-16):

#CRANK CRANK VR: UP 680k 1n
R222,"680k","R0402","C163456"
R226,
C211,"1n","C0402","C1523"
#CAM CAM HALL: DOWN DNP 1n
R220,
R224,
C209,"1n","C0402","C1523"
#VSS 2STEP: DOWN DNP 1n
R219,
R223,
C208,"1n","C0402","C1523"
#TPS TPS1: DOWN 680k 100n
R204,
R208,"680k","R0402","C163456"
C203,"100n","C0402","C307331"
#TPS2 AIN1: DOWN DNP 1n
R202,
R206,
C201,"1n","C0402","C1523"
#PPS PPS1: DOWN 680k 100n
R203,
R207,"680k","R0402","C163456"
C202,"100n","C0402","C307331"
#PPS2 AIN2: DOWN DNP 1n
R201,
R205,
C200,"1n","C0402","C1523"
#IAT IAT: UP DNP 100n
R213,
R217,
C207,"100n","C0402","C307331"
#AT1 VMAIN: EXT 100n
R212,
R216,
C206,"100n","C0402","C307331"
#CLT CLT: UP DNP 100n
R211,
R215,
C205,"100n","C0402","C307331"
#AT2 PAD: UP 4.7k 100n
R210,"4.7k","R0402","C25900"
R214,
C204,"100n","C0402","C307331"
#O2S WakeUP: DOWN 680k 100n
R238,
R242,"680k","R0402","C163456"
C217,"100n","C0402","C307331"
#O2S2 AFR: DOWN 680k 100n
R239,
R243,"680k","R0402","C163456"
C218,"100n","C0402","C307331"
#RES1 CAM VR: UP 680k 1n
R237,"680k","R0402","C163456"
R241,
C216,"1n","C0402","C1523"
#RES2 CAM VR ANALOG: UP DNP 1n
R240,
R244,
C219,"1n","C0402","C1523"
#RES3 CRANK VR ANALOG: UP DNP 1n
R231,
R235,
C215,"1n","C0402","C1523"
#MAP1 AIN3: DOWN DNP 1n
R228,
R232,
C212,"1n","C0402","C1523"
#MAP2 MAP: DOWN 10k 10n
R229,
R233,"10k","R0402","C25744"
C213,"10n","C0402","C15195"
#MAP3 MAP2: DOWN 10k 10n
R230,
R234,"10k","R0402","C25744"
C214,"10n","C0402","C15195"
#AUX1 TPS2: DOWN 680k 100n
R246,
R250,"680k","R0402","C163456"
C225,"100n","C0402","C307331"
#AUX2 PPS2: DOWN 680k 100n
R247,
R251,"680k","R0402","C163456"
C226,"100n","C0402","C307331"
#AUX3 AIN4: DOWN DNP 1n
R248,
R252,
C227,"1n","C0402","C1523"
#AUX4 FLEX: UP DNP DNP
R249,
R253,
C228,
#SENS1 D2: UP DNP 1n
R259,
R263,
C230,"1n","C0402","C1523"
#SENS2 D3: UP DNP 1n
R260,
R264,
C231,"1n","C0402","C1523"
#SENS3 D4: UP DNP 1n
R261,
R265,
C232,"1n","C0402","C1523"
#SENS4 D5: UP DNP 1n
R262,
R266,
C233,"1n","C0402","C1523"
#KNOCK KNOCK: DOWN 680k 1n
R221,
R225,"680k","R0402","C163456"
C210,"1n","C0402","C1523"
#D1 HALL1: UP DNP 1n
R124,
R136,
C143,"1n","C0402","C1523"
#D2 TLS115_PG: UP DNP 1n
R126,
R137,
C144,"1n","C0402","C1523"
#D3 HALL2: UP DNP 1n
R132,
R138,
C145,"1n","C0402","C1523"
#D4 HALL3: UP DNP 1n
R135,
R139,
C146,"1n","C0402","C1523"

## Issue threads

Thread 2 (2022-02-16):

C4 digital input to support more modes

rusefillc, 2022-02-16:
At the moment C4 digital input is hall only

@ElDominio is asking for that to support 12v/5v/gnd input

@andreika-git do we already support 12v/5v/gnd with software-configurable pull-up?

andreika-git, 2022-02-16:
> @andreika-git do we already support 12v/5v/gnd with software-configurable pull-up?

Currently "C4" has no software-configurable pull-up, it has only 5v fixed pull-up but is fully 12v-tolerant (as well as other inputs).

rusefillc, 2022-02-18:
See https://github.com/rusefi/alphax-2chan/issues/32

ElDominio, 2022-12-03:
Close?

Closed 2022-12-03.

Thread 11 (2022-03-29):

rev A test log

rusefillc, 2022-03-29:
works from +12 as arrived from JLC

rusefillc, 2022-03-29:
```
2022-03-29_17_17_18_586: EngineState: confirmation_bluetooth_jdy 115200 alphax 1234:32
2022-03-29_17_17_18_586: EngineState: *** Bluetooth module setup procedure ***
2022-03-29_17_17_18_587: EngineState: !Warning! Please make sure you're not currently using the BT module for communication (not paired)!
2022-03-29_17_17_18_587: EngineState: TO START THE PROCEDURE: PLEASE DISCONNECT YOUR PC COM-PORT FROM THE BOARD NOW!
2022-03-29_17_17_18_587: EngineState: After that please don't turn off the board power and wait for ~15 seconds to complete. Then reconnect to the board!
2022-03-29_17_17_19_471: EngineState: Sleeping...
2022-03-29_17_17_20_436: EngineState: Restarting at 9600
2022-03-29_17_17_20_546: EngineState: Sending AT+VERSION
2022-03-29_17_17_21_521: EngineState: Running at 9600
2022-03-29_17_17_21_522: EngineState: Sending AT+BAUD8
2022-03-29_17_17_21_631: EngineState: received 2 byte(s) 1 [+][O]
2022-03-29_17_17_22_609: EngineState: Restarting at 115200
2022-03-29_17_17_22_609: EngineState: Sending AT+NAMEalphax
2022-03-29_17_17_22_718: EngineState: received 2 byte(s) 1 [+][O]
2022-03-29_17_17_23_701: EngineState: Running at 115200
2022-03-29_17_17_23_702: EngineState: Sending AT+PIN1234
2022-03-29_17_17_24_790: EngineState: Restarting at 38400
2022-03-29_17_17_24_791: EngineState: SUCCESS! All commands (4 of 4) passed to the Bluetooth module!

```

rusefillc, 2022-03-29:
with R40 removed and 115 added have +5v made from +12v

rusefillc, 2022-03-30:
https://github.com/andreika-git/hellen-one/issues/148 reported

rusefillc, 2022-03-30:
for CAN sleep/wake up see https://github.com/rusefi/alphax-4chan/issues/13

rusefillc, 2022-03-31:
baro works - reads 101kPa

ETB works!!!

(I still hate soldering ETB chips - first it worked for a second and scared shit out of me. works much better once more properly soldered)

andreika-git, 2022-03-31:
> for CAN sleep/wake up see #13

A proper (hopefully?) CAN wakeup with an additional inverted buffer is on 2ch-revC, not on 4ch-revA.

rusefillc, 2022-04-26:
https://rusefi.com/online/index.php?vehicleName=La+Mitsubicha&user_id=675&sorts[uploadedMsq]=-1&sorts[uploadedLog]=-1

https://youtu.be/egtDQsMDQqs

Closed 2022-05-15.

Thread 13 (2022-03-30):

rev A: CAN sleep/wake is sporadic

rusefillc, 2022-03-30:
4chan with 4 wires:
GND, +12, CAN_H, CAN_L

CanHacker device "shot" single CAN sending feature

```
canRxAdd(0x570)
function onCanRx(bus, id, dlc, data)
	print('got CAN id=' ..id ..' dlc=' ..dlc)
	id11 = id % 2048
	if id11 == 0x570 then
		mcu_standby()
	end
end
```

PROBLEM:
60% of the times 4chanA goes to sleep with first 0x570 packet and wakes up on next 0x570

40% of the times 4chanA would reboot on incoming 0x570 packet

@andreika-git did you say we have something inverting something somewhere? cannot find it

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

andreika-git, 2022-03-31:
A proper (hopefully?) CAN wakeup with an additional inverted buffer is on 2ch-revC and h81hd-revA, not on 4ch-revA.

rusefillc, 2022-03-31:
which makes me wonder how come it works at 60% :)

rusefillc, 2022-06-10:
no time to investigate rev A configuration

Closed 2022-06-10.

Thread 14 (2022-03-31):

Vertical USB

rusefillc, 2022-03-31:
Considering case layout vertical would work better

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

rusefillc, 2022-03-31:
@ElDominio what do you think?

Vertical usb is a bit more fragile, probably no space for usb-b?

ElDominio, 2022-03-31:
While I understand, I typically drill a hole for people demanding access, it can be done but I don't know if it's worth it.

USB-B is the printer one right?

rusefillc, 2022-03-31:
yep, USB-B is the printer one

vertical connector is about 14x14mm which we do not have

ElDominio, 2022-03-31:
Yeah, if we can switch to type B vertical, it could be done, but if we keep miniusb I'd say keep horizontal.

andreika-git, 2022-03-31:
Unfortunately, it's highly unlikely that we can find more space to fit the USB-B-Vertical connector without total rearrangement of the whole board... Unless we remove the left mounting hole (near the bluetooth module)...

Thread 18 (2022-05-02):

Q3 long term fix BOM or schematics?

rusefillc, 2022-05-02:
We would need same as https://github.com/rusefi/alphax-2chan/issues/52

andreika-git, 2022-06-10:
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

Done
https://github.com/rusefi/alphax-4chan/commit/a3c0af0193ebfe586d35963ddcb781002348c70c

rusefillc, 2022-06-10:
@mck1117 wanna review?

mck1117, 2022-06-14:
simulation says with the existing circuit we can't exceed about -10.4 volts V_gs on Q3, up to 30v supply voltage.

The pullup functions correctly above ~9.5 volts battery voltage, so we're fine there too!

Closed 2022-06-14.

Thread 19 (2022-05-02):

Q3 hardware mod for rev A and rev B

rusefillc, 2022-05-02:
See https://github.com/rusefi/alphax-2chan/issues/53

andreika-git, 2022-05-03:
There is also a suggestion to swap p-channel mosfets for vishay SI2347DS-T1-BE3 is similar but has 20V max V_gs part:
* Q3, Q4, Q5, Q16, Q17, **Q31, Q32**.

rusefillc, 2022-05-04:
@andreika-git do we have JLCPBC suggestions maybe it's not too late to replace part in the current order

andreika-git, 2022-05-04:
SI2347DS is perfectly available on JLC: C710065 or C145002

rusefillc, 2022-05-10:
I've ordered all qty 14 of SI2347DS-T1-BE3 available on Mouser

need more to fix the 10 units of rev A I am receiving

rusefillc, 2022-05-11:
@andreika-git says 726-BSS308PEH6327

rusefillc, 2022-05-19:
@andreika-git just to confirm that Q18 is NOT affected?

andreika-git, 2022-05-19:
> @andreika-git just to confirm that Q18 is NOT affected?

Yes, it has 3.3v which is < 12v

Closed 2022-07-26.

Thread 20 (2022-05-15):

was [rev B test log] now let's restore that test board

rusefillc, 2022-05-15:
does not DFU as arrived from JLC

This is different from https://github.com/rusefi/alphax-2chan/issues/47 since no USB power surge and a number of LEDs are ON, just no DFU

rusefillc, 2022-05-15:
With USB power, 3v regulator gets 3.6v input instead of expected 4.8v input

with 3.6v input 3v generator outputs about 0.1v

rusefillc, 2022-05-17:
keweisi usb detector says 1.6A

hottest area SEEMS to be between MCU module and VR module but hard to say with more precision :( i think back side gets cooler when I touch it, i take all the heat?

rusefillc, 2022-05-17:
3v regulator U101 seemed like the hottest part

I've removed U101 and consumption went down to 0.17A

rusefillc, 2022-05-17:
with U101 removed 3v to ground beeps, seems to be about 1 ohm

rusefillc, 2022-05-17:
found issue it was similar to Harley defect

root cause lack of automated validation https://github.com/andreika-git/hellen-one/issues/152

rusefillc, 2022-05-18:
it was a gerber issues with a via under  C461

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

Q: how happy is this ECU going to be without C461?

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

rusefillc, 2022-05-22:
gerber issue around Ign fixed by https://github.com/rusefi/alphax-4chan/commit/38b9e8fdefc0ad3ff9537dbe6887440f12287586

rusefillc, 2022-07-02:
three cuts total

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

rusefillc, 2022-07-11:
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

ElDominio, 2022-07-11:
I need to do this to revB 4chan I suppose?

rusefillc, 2022-07-11:
@ElDominio short answer is NO

ElDominio, 2022-12-03:
Close?

Closed 2022-12-03.

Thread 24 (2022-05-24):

ETB heat management: More vias under ETB chip? copper somewhere?

rusefillc, 2022-05-24:
@mck1117 suggests more vias under ETB chip

can we actually have huge holes to facilitate soldering with limited tools?

4chan at the moment
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

probably Proteus
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

rusefillc, 2022-06-09:
@ElDominio reports issues during calibration, we need an incremental improvement.

```
overheat
a few cars have had issues BUT, not driving
couldn't the underside have a bit of copper to solder it onto for heat dissipation?
```

My question: can we make LARGE vias like 1.5mm to give a chance to solver through back side to make soldering simpler?

ElDominio, 2022-06-09:
About soldering, I have a guy that solders them PERFECTLY now. This improved the situation but did not fix it.

mck1117, 2022-06-09:
Proteus has 3 ground planes, and tons of vias under the chips, and has no overheating problem.

rusefillc, 2022-06-10:
@mck1117 @Qwerty-OFF please review

rusefillc, 2022-06-11:
@andreika-git says that connected polygon could make it too hard to solder in terms of heat requirmen

Closed 2022-06-11.

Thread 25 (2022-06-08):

Main Connector Fitment issues - see picture

ElDominio, 2022-06-08:
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

The connectors are ever so slightly too close together, making the connectors bend upwards in the middle. They need to be space a tiny fraction of an mm

rusefillc, 2022-06-09:
Million dollar question: how much do we move let's say grey connector?

I have both "legacy" and "neo" 4chan in my hands and maaaaaaaaybe "legacy" is a bit easier to install in the case

@ElDominio I have no idea how to measure the amount we need to move the grey connector (randomly picking which one to move)

0.3mm?

@andreika-git how do gerbers compare between "legacy" and "neo"? is there _any_ difference to justify minor difference which I _maybe_ feel?

ElDominio, 2022-06-09:
I'm thinking maybe split them both, move each like .15mm or so. It's very tiny, but it doesn't allow the top plate to be fully screwed into place, which is a bit problematic

andreika-git, 2022-06-09:
> @andreika-git how do gerbers compare between "legacy" and "neo"? is there _any_ difference to justify minor difference which I _maybe_ feel?

The original gerbers (1200 dpi):

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

The 4ch-revb gerbers (1200 dpi):

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

The difference (1200 dpi):

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

andreika-git, 2022-06-09:
Let's check the bottom-left hole:

1) The original gerbers:
  Origin corner: (91.3, -152.2), Hole location: (96.9, -142.65)
  **Coordinates: 5.6 9.55**
  **Diameter: 1.8**

2) 4ch-revB:
  Origin corner: (0, 114.7), Hole location: (9.64946, 109.101)
  **Coordinates: 5.599 9.64946**
  **Diameter: 1.50114**

The max difference between the coordinates is 9.64946-9.55 = **0.1 mm**
Visually I see the max. difference ~5 pixels, which also means ~0.1 mm @ 1200 dpi.

I think the main difference is not coordinates but hole size: let's make 1.8 mm instead of 1.5 mm

P.S. Are all connectors the same?

rusefillc, 2022-06-10:
both connectors overall outer size where it matters: 91.8mm
inner width of relevant case region: 93.1mm

let's move both connectors apart from each over, let's move each by 0.35mm for overall width change of 0.7mm

let's NOT change hole diameter there is no reason for that

andreika-git, 2022-06-10:
done.
https://github.com/rusefi/alphax-4chan/commit/a3c0af0193ebfe586d35963ddcb781002348c70c

We still have some space on the edge:
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

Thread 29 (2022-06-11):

rev C - low stock and not cheap SN74LVC2G17DCKR C50714

rusefillc, 2022-06-11:
any cheaper than $3 and qty 103 C50714 alternatives?

http://www.ti.com/cn/lit/gpn/sn74lvc2g17

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

rusefillc, 2022-06-11:
@andreika-git do we have options in same or smaller packages?

andreika-git, 2022-06-11:
The same package, the cheapest but low stock: C94189
The same package, rather expensive but more stock: C80500

rusefillc, 2022-06-11:
i now own x65 of C94189

rusefillc, 2022-06-11:
Dave mentions [C458779](https://jlcpcb.com/parts/componentSearch?isSearch=true&searchTxt=C458779)

this nexperia partis cheap ($0.16) on a reel.  depending on how many you use, may be worth global sourcing  supply sucks right now, but sourceengine has a ton. mouser has 80ish

extreme part shortage of all parts in this package.  I would be looking at alternative packages or possibly a quad or single vs. dual buffer

rusefillc, 2022-06-11:
New separate issue https://github.com/rusefi/alphax-4chan/issues/32

mck1117, 2022-06-14:
C80500 WILL NOT work - not rated for use of the high side diodes

mck1117, 2022-06-14:
[C458779](https://jlcpcb.com/parts/componentSearch?isSearch=true&searchTxt=C458779) will not work since it's 3.3v only, and has no high side diodes either.

mck1117, 2022-06-14:
Actually - the original part C50714 doesn't work either since it has no high side diodes!

mck1117, 2022-06-14:
we must use C94189

rusefillc, 2022-06-14:
qty 500 of 74HC2G17GW,125 https://jlcpcb.com/parts/componentSearch?isSearch=true&searchTxt=C94189 has arrived to NJ

Closed 2022-06-14.

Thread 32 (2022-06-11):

Test +12v Hall input on rev A or B

rusefillc, 2022-06-11:
Suddently there is a concurn that maybe 4chan rev A and B does not support +12v Hall Input. We need to either fix boards or attempt potentially destructive test

rusefillc, 2022-06-11:
So I configure Hall mode on 4chan rev A or B board, feed +12v from 1A power supply.

Worst case scenario how much of the board would we fry? is there a chance to fry stm32?

@ElDominio just FYI

rusefillc, 2022-06-13:
@andreika-git what is the bad case scenario in terms of specific board damage?

andreika-git, 2022-06-13:
> @andreika-git what is the bad case scenario in terms of specific board damage?

The worst case scenario is U2/U5 failing and passing +12V directly to the digital inputs of the mcu, and it would fail too (5v-tolerant pins of STM32 don't have overvoltage protection diodes).

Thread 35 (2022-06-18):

C7/F7 shown as ADC

ElDominio, 2022-06-18:
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

I think that's wrong, is it not?

rusefillc, 2022-06-18:
it sounds like technically crank and cam could be used as analog @andreika-git please confirm

```
  - pin: C7
    # H144_IN_CAM
    id: [A6, A6, EFI_ADC_6]
    class: [event_inputs, switch_inputs, analog_inputs]
    function: Camshaft HALL Sensor or Generic Digital Input
    type: hall
    ts_name: C7 - CAM Hall/Digital
    color: brown
```

@ElDominio please clarify if you would rather hide to reduce potential confusion

ElDominio, 2022-06-18:
If they can, that would be cool, but aha, if they can't they shouldn't be listed today. I had a guy ask me if he could use it as such today lol

andreika-git, 2022-06-18:
Yes, C7 can be used as a generic analog input.

F7 can be also used (in theory), but it's special:
1) it can measure 12V voltage (and more) and thus it has a voltage divider, so we need to modify the firmware to support it as a generic input (add a divider coefficient).
2) VIGN is currently required by the firmware for main relay and power control.
So currently it's not recommended to use F7 as an alternative analog input, although it's possible in the hardware (with a custom firmware).

mck1117, 2022-06-18:
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

It's also on adc3 so we can't actually use it without significant architectural changes. Aka, you can't use it.

andreika-git, 2022-06-18:
> It's also on adc3 so we can't actually use it without significant architectural changes. Aka, you can't use it.

pin C7 = IN_CAM_HALL = IN_CAM = AIN19 = A19 = PA6 = ADC12_IN6
Aka, you can use it.

rusefillc, 2022-07-26:
@ElDominio shall we close this one or still anything actionable?

ElDominio, 2022-07-26:
Still not clear if can use or not as ADC

mck1117, 2022-07-26:
As far as I can tell from the schematic, you can use it as analog.

rusefillc, 2022-07-26:
@ElDominio ^^^

Closed 2022-07-26.

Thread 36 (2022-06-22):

Main relay control not working properly

ElDominio, 2022-06-22:
I can't get a log but I can get a video. Main relay control works once, then after turning the key back on, the ECU seems to hang, I cannot connect to it through USB until I unplug it from the car and plug it back in`
More testing:
if i keep the laptop plugged in, key off, then unplug USB, the ecu shuts off;
if the laptop is unplugged, th ecu will stay turned on, and the next time i connect it is unresponsive until i fully disconnect the main harness and reconnect

rusefillc, 2022-06-22:
any board or specific board?

are you personally there?

ElDominio, 2022-06-22:
Yep, it's the Lancer I am testing. RevA 4Chan

rusefillc, 2022-06-22:
Thank you for answering the second question!

Do you have more 4chan units you can try on same vehicle? i.e. is this issue specific to one board or any board is affected?

ElDominio, 2022-06-22:
I do, I'll do that on Thursday too

ElDominio, 2022-06-23:
About this:

Apparently, when battV is below a certain point, main relay control fails. Charged the battery up and now it's working as expected

ElDominio, 2022-06-23:
For some reason, when battery voltage was about 10.8v, the ECU would just hang. Now that the battery is charged it works as expected

rusefillc, 2022-06-28:
@ElDominio close this one?

ElDominio, 2022-06-28:
Will run some more tests tomorrow and comment back on this

ElDominio, 2022-07-06:
Close this since it was discovered this is a Lua issue, not a 4chan issue.

rusefillc, 2022-07-06:
See https://github.com/rusefi/rusefi/issues/4322

Closed 2022-07-06.

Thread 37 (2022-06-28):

4chan rev C test log

rusefillc, 2022-06-28:
powers on!

5000 rpm injector test see https://rusefi.com/forum/viewtopic.php?p=45716#p45716

rusefillc, 2022-06-28:
testing tach out

self stim
got 2.5v output and frequency

switched to 12v tach out
got 3.3v FAILED?

rusefillc, 2022-06-28:
R47 replaced with 470 ohm
voltage across is 0.9v now

tach output 7.4v

rusefillc, 2023-03-14:
rev C is a success

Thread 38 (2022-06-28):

Tach voltage not +12v

rusefillc, 2022-06-28:
with D1 removed voltage is 9.9v

with R46 value lowered to 470 tach voltage 11.5v

andreika-git, 2022-07-23:
https://github.com/rusefi/alphax-4chan/commit/4de32993da84c7dde138b381038f24e7c7060564

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

ElDominio, 2023-02-02:
RevE still not ok

In 12v mode, still spitting out around 4v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

rusefillc, 2023-02-02:
Первый шаг отпаять D1 или D9 (светодиод TACH)

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

Второй посмотреть осциллографом что происходит на левой ноге R47

rusefillc, 2023-02-02:
Baseline test in NJ

1R load
actual result:
tach LED does not blink
0v<>1v square wave with "5v" tach mode
0v<>2v square wave with "12v" tach mode

rusefillc, 2023-02-02:
removed D9
nothing has changed - same 0/1 or 1/2v levels

left side of R47 constant 12v

rusefillc, 2023-02-02:
1K load was a BAD TEST

without any load, with D9 removed I have happy 0v/+12v on tach output!

now going to return D9 since did not test without load :(

rusefillc, 2023-02-02:
@ElDominio it seems to work fine on bench

@Qwerty-OFF says it could be about your specific resistance on specific tach.

@ElDominio can you please try with tach disconnected - would it be 9v or 12v without tach?
@ElDominio can you measure tach resistance to GND?

ElDominio, 2023-02-04:
Hi, in the local tests I have done:

1) With nothing connected, it behaves as expected
2) With an older 12V tach, voltage drops as seen on the scope, tach does not move
3) Works fine with logic based tachs (5v), since they seem to only use the square wave to drive a motor
4) In 12V cases, we usually use the 5v output to drive a N2222 transistor pulled up to 12v, which then is used to drive the tacho. This works fine

rusefillc, 2023-03-16:
@ElDominio are you looking for any changes on rev G like making the N2222 official right on the board? not sure if things would stay configurable

@ElDominio the safest option would be to provision for maybe even through hole N2222 right on 4chan but have it not populated by default, would you like that?

ElDominio, 2023-03-16:
Having space for a 2222 THT, sounds at least like a _decent_ fix to make it _somehwat_ configurable, and I'd like it in all boards, I had totally forgotten about this

Qwerty-OFF, 2023-03-18:
Now we have a transistor like N2222 pulled up to 5V. It can also be pulled up to 12V by additional control signal from MCU. What needs to be added?
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

ElDominio, 2023-03-19:
So when I have issues with 12v tach, I usually use the Tach output on the ECU to drive a 2222 pulled up to 12V on the output, and then this produces a clean 12v square wave

ElDominio, 2023-03-19:
Pullup is 1k

Qwerty-OFF, 2023-04-02:
Configurable pullup:
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
Low-side MOSFET:
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

rusefillc, 2023-04-02:
Reopening to game more notes

ElDominio, 2023-07-23:
RevG can change voltages just fine

Closed 2023-07-23.

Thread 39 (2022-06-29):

randomly does not turn off

rusefillc, 2022-06-29:
https://youtu.be/YtoW3d-4EBI

rusefillc, 2022-06-29:
please connect laptop please tell battery voltage gauge with ign key off

if ign key is off I can offet a Lua hack:

a lua script which
a) waits for battery to go above 11
b) if battery is ever below 5 after it was above 11, put rusEFI to sleep. that would turn of main relay and address back feed

that's probably a hack?

ElDominio, 2022-06-29:
Will update on Thursday then

rusefillc, 2022-06-29:
something along these lines

```
shallSleep = Timer.new()

-- we want to turn on with hardware switch while ignition key is off
hadIgnitionEvent = false

function onTick()

	if vbatt > 11 then
		-- looks like we have ignition key do not sleep!
		shallSleep : reset()
		hadIgnitionEvent = true
	end

	if hadIgnitionEvent and shallSleep : getElapsedSeconds() > 3 then
		-- looks like ignition key was removed
		mcu_standby()
	end

end

```

mck1117, 2022-06-29:
@rusefillc wait, isn't this just the main relay control logic? It turns the main relay off if the ignition voltage drops.

rusefillc, 2022-06-29:
could be :(

TL,DR: i have same/similar drama on proteus. on Proteus I have CAN-based ignition key that helps

mck1117, 2022-06-29:
Where is the power coming from? What pin still has power that we liberate by turning off the main relay?

Also, log?

ElDominio, 2022-06-29:
Log can't show anything imo, if the key is turned off with the laptop, you can see voltage change, but the ecu behaves as expected and shuts off when you disconnect USB.

ElDominio, 2022-06-29:
If the ECU gets stuck on and keyed off, you connect USB and the ECU is just hung, USB Device Descriptor Request Failed shenanigans

mck1117, 2022-06-29:
> Log can't show anything imo, if the key is turned off with the laptop, you can see voltage change, but the ecu behaves as expected and shuts off when you disconnect USB.

If you can see the ignition voltage change and the ECU doesn't turn off the main relay, this is a bug.

mck1117, 2022-06-29:
> b) if battery is ever below 5 after it was above 11, put rusEFI to sleep. that would turn of main relay and address back feed

The main relay control code is supposed to be doing this already

ElDominio, 2022-06-30:
I'm with the car

Voltage detects perfectly but problem continues; again i Can't log it, since with the laptop it can't be replicated

rusefillc, 2022-06-30:
is connector easy to depin? do you know how to depin connector

can you disconect as many low side driver wires as possible? idle? vvt? maybe even relays etc?

i.e. what's the minimal set of wires to reproduce the problem?

and you say it's sporadic not 100% reproducible? :(

rusefillc, 2022-06-30:
crazy ideas:

lua script to turn off if no RPM for 60 seconds?

ElDominio, 2022-07-01:
https://drive.google.com/drive/folders/1_tZcS8Qz7JpopSBae-BIwZ7rOK1sBMPq?usp=sharing

Videos of the issues. @mck1117 helped me trace this back to a Lua issue causing a boot loop.
My Lua code is here
https://gist.github.com/ElDominio/8385f846d1e0bcc8d2e2569ff62d45e9

rusefillc, 2022-07-01:
Current status unclear.

Is this issue resolved? Is this issue not resolved but solegow narrowed down to specific lua script?

mck1117, 2022-07-02:
Not resolved but it's a little more data. Alpha and I are still looking in to it.

ElDominio, 2022-07-02:
Yeah, right now @mck1117 is waiting on me till I can connect to the ECU with my STlink

I have an STlink V2 btw, not V3, obviously ebay clone. This works right? Where does it connect to?

rusefillc, 2022-07-03:
Г. Б

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

rusefillc, 2022-07-03:
you have three options https://github.com/rusefi/rusefi/wiki/Tag-Connect-TC2030 describes all three

most proper - order and solder FTSH-105-01-F-DV-007-K connector and v3 which is cheap

proper with zero soldering: v3 + proper tc2030 cable for v3

cheapest: v2 + ghetto tc2030 based on eBay TC2030-MCP-NL with phone jack cut off

rusefillc, 2023-03-14:
@ElDominio how can I reproduce at home? Shall we close or else?

ElDominio, 2023-03-14:
Close for now, Haven't really run into it

Closed 2023-03-14.

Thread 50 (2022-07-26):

VND7NV04TR-E 60ohm/6A instead of VND14NV04 35ohm/12A

rusefillc, 2022-07-26:
VND7NV04TR-E
C155605

to replace hand assembled VND14NV04 C155647

rusefillc, 2022-07-26:
@andreika-git please confirm pinout/shape match

@andreika-git please confirm that we are OK with extra resistance

ElDominio, 2022-07-26:
I thought we were waiting to see if JLC got VND14s back in stock?

The eBay sourced ones seem to work well too, I'd rather have the peace of mind of the 14s if possible

rusefillc, 2022-07-26:
a) there is no way that the smaller pins hold even 6A, i bet same applies to larger pins
b) JLC UI gives me an option to preirder VND14 C155647 but those are $4.5 instead of $0.60 ebay, i.e. $40 extra per board

ElDominio, 2022-07-26:
I can have them from eBay and solder here, VND14 is not too difficult to solder
most VND outputs are on the edge pins which hold about 10A

The most important thing is being able to hold 4 injectors per channel cause trust me people will do that

Closed 2022-07-26.

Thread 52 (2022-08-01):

what feedback can we read how

rusefillc, 2022-08-01:
https://www.st.com/resource/en/datasheet/vnd14nv04.pdf

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

Q1: do we get only "1 bit of fault feedback" effectively "shorted to power" and nothing else? no way to detect missing load/injector/solenoid?

Q2: would stm32 be able to read feedback on current alphax-4chan schematics?

Qwerty-OFF, 2023-03-15:
Q1:  only "1 bit of fault feedback" effectively "shorted to power" and nothing else
Q2: No, an additional feedback line to MM module is required.

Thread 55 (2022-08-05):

two-solenoid IAC dos not work

rusefillc, 2022-08-05:
https://rusefi.com/online/view.php?msq=1138&dialog=idlehw

think there is a problem with two wire idle on 4chan

[andrey](https://app.slack.com/team/U4PVDN5L7)
  [9:00 PM](https://rusefi.slack.com/archives/C4Y7HA6NM/p1659661238635819)
are you trying two idle IAC for first time?

[AlphaX](https://app.slack.com/team/U02PS3897M3)
  [9:00 PM](https://rusefi.slack.com/archives/C4Y7HA6NM/p1659661259578909)
yep
[9:01](https://rusefi.slack.com/archives/C4Y7HA6NM/p1659661279983469)
i think there is some flyback or something, if they are both connected, the idle valve doesn't move
[9:01](https://rusefi.slack.com/archives/C4Y7HA6NM/p1659661285007319)
and both bulbs are equally lit
[9:01](https://rusefi.slack.com/archives/C4Y7HA6NM/p1659661293782369)
if i disconnect one, it works in the direction that is still connected

[andrey](https://app.slack.com/team/U4PVDN5L7)
  [9:01 PM](https://rusefi.slack.com/archives/C4Y7HA6NM/p1659661316103349)
"they are both connected"
[9:02](https://rusefi.slack.com/archives/C4Y7HA6NM/p1659661339052339)
any chance you are talking about a three wire IAC?

[AlphaX](https://app.slack.com/team/U02PS3897M3)
  [9:03 PM](https://rusefi.slack.com/archives/C4Y7HA6NM/p1659661384058059)
yes that
[9:03](https://rusefi.slack.com/archives/C4Y7HA6NM/p1659661388709489)
two wire iac is fine
[9:03](https://rusefi.slack.com/archives/C4Y7HA6NM/p1659661396550159)
i forgot three = 2 control wires

[Simon - FutureProof Performance](https://app.slack.com/team/UF9NQSX8T)
:palm_tree:  [9:05 PM](https://rusefi.slack.com/archives/C4Y7HA6NM/p1659661536647589)
Double solenoid IAC

[AlphaX](https://app.slack.com/team/U02PS3897M3)
  [9:07 PM](https://rusefi.slack.com/archives/C4Y7HA6NM/p1659661634289279)
yes
[9:07](https://rusefi.slack.com/archives/C4Y7HA6NM/p1659661651307179)
i'm going to install diodes on it later to see if it started working correctly

[andrey](https://app.slack.com/team/U4PVDN5L7)
  [9:08 PM](https://rusefi.slack.com/archives/C4Y7HA6NM/p1659661693689269)
that's all very weird
[9:08](https://rusefi.slack.com/archives/C4Y7HA6NM/p1659661704189649)
"install diodes" huh
[9:09](https://rusefi.slack.com/archives/C4Y7HA6NM/p1659661751131579)
with a lot of respect your tune contains SO much of data that not providing it is a crime

[Matthew Kennedy](https://app.slack.com/team/U80K9BYVD)
  [9:09 PM](https://rusefi.slack.com/archives/C4Y7HA6NM/p1659661765451389)
There are two camps on how to control a three wire
[9:09](https://rusefi.slack.com/archives/C4Y7HA6NM/p1659661778156979)
Either you energize both, or you only ever do one at a time

[andrey](https://app.slack.com/team/U4PVDN5L7)
  [9:10 PM](https://rusefi.slack.com/archives/C4Y7HA6NM/p1659661808609069)
image.png
image.png

:+1:
1

[AlphaX](https://app.slack.com/team/U02PS3897M3)
  [9:10 PM](https://rusefi.slack.com/archives/C4Y7HA6NM/p1659661815094929)
[@andrey](https://rusefi.slack.com/team/U4PVDN5L7)
 it's on rusefi online

[andrey](https://app.slack.com/team/U4PVDN5L7)
  [9:10 PM](https://rusefi.slack.com/archives/C4Y7HA6NM/p1659661816924579)
i do not comprehend "install diodes"
[9:10](https://rusefi.slack.com/archives/C4Y7HA6NM/p1659661828472849)
:disappointed:

[AlphaX](https://app.slack.com/team/U02PS3897M3)
  [9:10 PM](https://rusefi.slack.com/archives/C4Y7HA6NM/p1659661844551869)
image.png
image.png

[andrey](https://app.slack.com/team/U4PVDN5L7)
  [9:11 PM](https://rusefi.slack.com/archives/C4Y7HA6NM/p1659661888713829)
https://rusefi.com/online/view.php?msq=1138&dialog=idlehw

rusefi.comrusefi.com
[rusEFI online](https://rusefi.com/online/view.php?msq=1138&dialog=idlehw)
rusEFI tune file sharing site
New

[Matthew Kennedy](https://app.slack.com/team/U80K9BYVD)
  [9:11 PM](https://rusefi.slack.com/archives/C4Y7HA6NM/p1659661907662279)
I see diodes

rusefillc, 2022-08-05:
@ElDominio i need the part number so that I could get this stuff here, I can solder some wires to connector hopefully

ElDominio, 2022-08-22:
On another 2 wire IAC, it seemed to work just fine (Toyota) , this might be case-by-case

ElDominio, 2022-12-03:
Close as i have used two wires successfully now

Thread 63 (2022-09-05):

What component to remove to ECU does not stay powered with a constant 12V source on an output

ElDominio, 2022-09-05:
On the PNP unit I made for Lancer X, A/C Clutch control is connected to F1 (Idle2). On the revA 4chan I was instructed to remove a component to make the ECU shut down properly, but I don't remember which one it is. Now that I am swapping to RevC I need to remove it again for the same effect.

rusefillc, 2022-09-05:
@mck1117 were you involved with this? Do you recall what was this about?

Would be nice to get to the more bottom bottom of this :)

ElDominio, 2022-09-05:
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

rusefillc, 2022-09-05:
@ElDominio is this A/C clutch PWM or on/off?

Anyway this or similar has happened enough of times that it needs to be understood more completely. Why does it happen for some outputs on some vehicles but no on others?

I am sure I had something like this on NB2 miata VVT, I am sure that I have back-feed on my Passat B6

@andreika-git @Qwerty-OFF @mck1117

ElDominio, 2022-09-05:
On/Off
Lancer 2009 N/A

The clutch relay has 12v at all times, if D51 is not removed, the ECU gets 12V from this output and turns on. Removing D51 removes this bad behavior, but probably gives problems with PWM. Since this output does not need to be PWM'd, this is fine.

rusefillc, 2022-09-05:
We are lucky here this time but there is the wider pattern.

Is this about A/C being connected to battery directly not sitting behind main relay?

rusefillc, 2022-09-05:
https://github.com/rusefi/rusefi_documentation/blob/master/OEM-Docs/Mitsubishi/2009-Lancer-Enginers-2L-turbo-2L-NA-2.4L-NA.pdf

ElDominio, 2022-09-05:
Stupid Github phone app

Yes, it is because what you said

ElDominio, 2022-12-03:
Can be closed

ElDominio, 2023-11-22:
@rusefillc @Qwerty-OFF what is the equivalent of d51 in revH?

Qwerty-OFF, 2023-11-22:
D66 for IDLE2 / F1 pin

rusefillc, 2024-02-27:
https://github.com/andreika-git/hellen-one/issues/368

Closed 2022-12-03.

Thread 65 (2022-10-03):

standby power consumption is still 64mA

rusefillc, 2022-10-03:
standby lowers power consumption of 4chanE without VND14 without MAP sensor from 99 to 65mA

one day we shall get much closer to 5mA

rusefillc, 2022-10-03:
that includes three bright green LEDs and two dim white LEDs

rusefillc, 2023-03-14:
Would be addressed as mm issue

Closed 2023-03-14.

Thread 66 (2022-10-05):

Mechanical improvements for MAP sensor footprint considering SD card on back

rusefillc, 2022-10-05:
We have some boards with MAP pulled off

only three of eight pads are actually used for anything

what tricks like vias and more metal can we try to increases our mechanical chances?

rusefillc, 2022-10-05:
@ElDominio any chance to see photos of damanges PCBs?

rusefillc, 2022-10-05:
@andreika-git please check datasheet if we can GND or else currently disconnected pads

ElDominio, 2022-10-05:
Will upload later today i think they're in my bag

ElDominio, 2022-10-07:
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

rusefillc, 2022-11-29:
Hot glue did not help these do not even survive shipping :(

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

@timbelom part of the problem is poor soldering?

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

mck1117, 2022-11-29:
is that broken solder joints, or pads torn off the board?

dron0gus, 2022-12-01:
Do not put high profile SMD components close to board edges.

rusefillc, 2022-12-01:
> Do not put high profile SMD components close to board edges.

plz remind why :)

mck1117, 2022-12-01:
> plz remind why :)

I seem to remember somebody recently had issues with tall components near the edge recently 🤔

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

ElDominio, 2022-12-01:
I assume that having it near the edge means it won't be inside the profile created by the connector and the edges of the board

rusefillc, 2023-01-22:
@Nadezhda-n please match latest 2chan maybe with larger center hole

Nadezhda-n, 2023-01-26:
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
Micro_SD_Card on the bottom.
I guess it needs to be moved?

rusefillc, 2023-01-26:
Ohhh let's do nothing for now that would be safest?

Nadezhda-n, 2023-01-26:
https://github.com/rusefi/alphax-4chan/tree/New_rev include this

ElDominio, 2023-01-27:
> Ohhh let's do nothing for now that would be safest?

Will MAP sensors still bruise easily?

rusefillc, 2023-01-29:
> Ohhh let's do nothing for now that would be safest?

@Nadezhda-n can we apply the copper change (connected NC pads and vias) but not the huge whole? i.e. can we only make progress which does not require SD card to be moved?

rusefillc, 2023-01-30:
2chan has another improvement and via to reinforce pads

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

Nadezhda-n, 2023-01-31:
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

Closed 2023-01-31.

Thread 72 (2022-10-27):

Hall input noise

rusefillc, 2022-10-27:
What are hardware causes of https://github.com/rusefi/rusefi/pull/4656?

rusefillc, 2023-01-10:
Related or not to https://github.com/rusefi/rusefi/issues/4918#issuecomment-1369794958 ?

rusefillc, 2023-01-10:
Is this related https://github.com/andreika-git/hellen-one/issues/245 https://github.com/andreika-git/hellen-one/issues/247

Qwerty-OFF, 2023-01-10:
> Is this related https://github.com/andreika-git/hellen-one/issues/245 https://github.com/andreika-git/hellen-one/issues/247?

Not related

Try to change C200 by 10nF or install 1-10nF here:
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

ElDominio, 2023-01-23:
@mck1117 , do these caps affect Hall/VR or only VR?

mck1117, 2023-01-23:
only vr

mck1117, 2023-01-23:
> @mck1117 , do these caps affect Hall/VR or only VR?

Wait sorry, which caps? The recently added caps in the VR module have nothing to do with hall inputs. The caps discussed in this thread I think are only hall.

ElDominio, 2023-01-23:
Ah now I see

@rusefillc , the car runs on C7 Cam hall input just fine using 4G93 cam only. The problem is using the 4(8) tooth crank (8 because both edges), which is wired to C3.

rusefillc, 2023-01-23:
@ElDominio I have no idea what are you trying to say.

@ElDominio are you saying that you are betting your kidney ghat we have no hardware issues?

mck1117, 2023-01-23:
Do we have an SD card log of this car? Whatever is or isn’t working?

ElDominio, 2023-01-23:
@rusefillc you gave me two options, but one seems irrelevant

@mck1117 4G93, I'm pretty sure i uploaded both logic analyzer and SD card

rusefillc, 2023-01-23:
It's a mess let me close ticket.

rusefillc, 2023-02-22:
We have major https://github.com/rusefi/rusefi/issues/5111 pain.

This ticket was closed since we were arguing on approach and if we even have a problem

@ElDominio has a Proteus and he has three spare sets of proteus harness connector kits to assemble multiple proteus harnesses. At some point I was asking for a comparison between 4chan and Proteus.

mck1117, 2023-02-22:
This board is still missing the caps seen in this comment on 8chan: https://github.com/rusefi/alphax-8chan/issues/28#issuecomment-1290187356

ElDominio, 2023-02-22:
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

I do not have manufacturing abilities myself, depend on others for this. Would be easier if i was provided with said test harness if design flaws need testing.

rusefillc, 2023-02-22:
> I do not have manufacturing abilities myself, depend on others for this. Would be easier if i was provided with said test harness if design flaws need testing.

very reasonable and very depressing. I am happy to go kill myself.

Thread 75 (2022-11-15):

ETB driver overheating

ElDominio, 2022-11-15:
In two cars already, when the car is keyed on ETB driver keeps having a very hard time to control ETB position (it even makes audible noises? wtf?) until it overheats and shutdown. Any way to improve cooling?

Temperature tested by touching the driver on key on

rusefillc, 2022-11-15:
@ElDominio what revisions?

We had a change between B and C open question if that was improvement or degradation. @mck1117 @Qwerty-OFF do we have potential for improvement?

rev A
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

rev B
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

rev C
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

ElDominio, 2022-11-15:
I think when JLC assembly started, they only solder pads, not chip to board

mck1117, 2022-11-15:
they've always soldered the thermal pad underneath, and we've never had a problem with the 9201 on proteus or MRE

ElDominio, 2022-11-18:
Tested between revB and revC, about 25F difference in temperatures

revB has no holes, revC does

mck1117, 2022-11-18:
> Tested between revB and revC, about 25F difference in temperatures (revB is cooler)

which is worse? B = C + 25 or C = B + 25?

ElDominio, 2022-11-18:
> > Tested between revB and revC, about 25F difference in temperatures (revB is cooler)
>
> which is worse? B = C + 25 or C = B + 25?

I said revB is colder lol, meaning C = B + 25

mck1117, 2022-11-18:
head empty no thoughts

ElDominio, 2022-11-18:
https://www.ebay.com/itm/185608066289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 ordered this too

mck1117, 2022-11-18:
Those won't do very much. The die is glued or soldered to the copper slug on the bottom, so you're going through a few mm of relatively thermally unconductive epoxy on the top. Can you try reflowing that chip with some more solder?

ElDominio, 2022-11-18:
I had the guy that does pro reflowing do them today and there was basically no change. Wouldn't the holes make it have less surface area for conducting heat so make it heat up quicker?

rusefillc, 2022-11-18:
@ElDominio i have an IR camera do you have an IR camera?

@ElDominio does it look like it's specific kind/model/vehicle ETB giving us problems or any ETB in general? I wonder what and how can I reproduce in NJ

ElDominio, 2022-11-18:
https://www.ebay.com/itm/174881539248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

That's what I measured with.

Right now I have it on 4 different setups and they all overheat.
Where should we be grounding the ECU? I always tell my kids to ground directly to battery but might that be causing issues?

rusefillc, 2022-11-19:
@ElDominio says this happens while engine is not running just ignition is ON

I am starting to wonder if that's tune / control strategy issue? Do we push these shut with 100% duty cycle or something? Need logs and tune.

rusefillc, 2022-11-21:
Linking just in case https://github.com/rusefi/rusefi/issues/4816

ElDominio, 2022-11-22:
This is a log of an ETB converted car we have at the shop, looks for resting position and fails a bit into the log: -> https://rusefi.com/online/view.php?log=1103

Same car trying to autocalibrate, I have tried a myriad of values on feed forward  and they don't make a difference -> https://rusefi.com/online/view.php?log=1104

If any videos are needed let me know; tune is tied to logs

ElDominio, 2022-11-22:
This is another ETB conversion with a fifth gen Camaro throttle, 2012 throttle. Catching this car failing is difficult since it _works_ most of the time, but it can someotimes give up randomly since it runs extremely hot.

Engine off key on -> https://rusefi.com/online/view.php?log=1105

running PID autocalibrate -> https://rusefi.com/online/view.php?log=1106 changed feed forward to be less positive in second run, you can still see it not getting exactly to 50

rusefillc, 2022-11-23:
@ElDominio can you please post tune + log of Ray's blue car, ignition on engine off?

My point is -  car at the shop I see crazy oscillation of duty cycle, I am comparing with nissan duty cycle chart and things are MUCH much smoother. Maybe energy magic happens when you change duty cycle that often that much?

shop car note crazy red line on top. Within two seconds it's constantly going -40% to +60%

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

now a log of my nissan sitting with engine off. Note how small is ETB Duty change when I am not touching pedal

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

@mck1117 how reasonable is my "energy"/total amount of change concern? Do we need some sort of volatility metric?

rusefillc, 2022-11-23:
Between VBat drop and ETB Duty volatility I am _guessing_ that ETB volatility is a much bigger concern.

Step one: need someone smart to voice their opinion on ETB Duty volatility and that's pretty much @mck1117 maybe @Qwerty-OFF @dron0gus @andreika-git

if/when we agree to blame PID settings next question would be why has auto calibrate failed. Is that a defect in code or could any power concerns be causing it.

Cherry on the case https://github.com/rusefi/rusefi/issues/4816 would that make a pattern of auto-calibrate being poor specifically on 4chan?! looks like next step would be to auto-calibrate same exact ETB on two different boards of different design. Let's see if @mck1117 would ask me to ship my test rig to him?

ElDominio, 2022-11-24:
Question: couldn't different operating states be defined for the throttle control system?

I've seen some ECUs that jitter for a bit when changing position, then basically "lock in" and stop jittering (LinkECU principally). I'd assume that have different duty limits for different states.

That's also how an ancient throttle controller I had made worked and I would say it worked pretty well, but that's anecdotal evidence. https://github.com/ElDominio/ETC_Control

rusefillc, 2022-11-24:
Answer: https://en.wikipedia.org/wiki/Moon_landing tells us that a lot of things are possible with proper resources.

Yes some (many? all?) h-bridges have "hold" state and it could be relatively easy to implement. But proper approach is first to identify the problem and then start addressing it.

I see very different behavior between your tune and my tune. I believe that first step is to explain it. If the problem is only with calibration we shall focus on calibration

Realistically next step is for me to reproduce the issue in NJ. What _exact_ part number ETB do we have problems with?

Another opinion: first we have to explain https://github.com/rusefi/rusefi/issues/4816

mck1117, 2022-11-24:
> Realistically next step is for me to reproduce the issue in NJ. What exact part number ETB do we have problems with?

Do we want to reproduce this instead in WA where I have the better test equipment to actually measure what’s going on?

mck1117, 2022-11-24:
Also, I don’t know what “hold state” means on an h bridge, but whatever it is, the tle9201 doesn’t have it.

rusefillc, 2022-11-24:
Best option is both WA and NJ :) @ElDominio we need exact part number to start acquiring matching stuff

ElDominio, 2022-11-24:
Bosch 99760511501

And

12629992

rusefillc, 2022-11-24:
That's porsche fancy?! How come?

 and LS less fancy :)

Let me cross-test same ETBs between 4chan and Proteus

rusefillc, 2022-11-25:
@ElDominio my bigger concern is not ETBs but connectors.

GM seems easiest and I have some VAG and Nissan pigtails for sure.

@mck1117 do you have a 4chan in WA or is it a 2chan you have?

rusefillc, 2022-11-26:
@ElDominio I have one or two logs and four part numbers for different ETBs. Do you see my problem?

ElDominio, 2022-11-27:
I offered to buy them so you can do it on your end, I was asked for logs and part numbers and I provided them lol

rusefillc, 2022-11-27:
@ElDominio please clarify which log is which ETB, which ETB is most problematic? Looks like GM is not horrible and we better start with a horrible one.

@ElDominio please confirm that you can source pigtails not just ETBs.

ElDominio, 2022-11-27:
I have the same pigtail problem but if i can source a pigtail + etb i will ship

rusefillc, 2022-11-27:
@ElDominio please clarify which log is which ETB, which ETB is most problematic? Looks like GM is not horrible and we better start with a horrible one.

rusefillc, 2022-11-27:
#4832 has convinced me that we have a calibration error here with potential for smarter error detection

I guess that #4833 is the next step

ElDominio, 2022-11-27:
> @ElDominio please clarify which log is which ETB, which ETB is most problematic? Looks like GM is not horrible and we better start with a horrible one.

1103  and 1104 are the most problematic, Bosch throttle body log.

Correct, GM is not horrible. Takes sometimes about a half hour to fail. Bosch fails almost instantly

rusefillc, 2022-11-29:
@ElDominio my Nissan logs are at https://rusefi.com/forum/viewtopic.php?p=46623#p46623 and https://rusefi.com/forum/viewtopic.php?p=46624#p46624

rusefillc, 2022-11-30:
over the phone discussion #79

rusefillc, 2022-11-30:
user error/software error https://github.com/rusefi/rusefi/issues/4832#issuecomment-1331639530

Closed 2022-11-30.

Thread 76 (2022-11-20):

Time to remove jumpers

rusefillc, 2022-11-20:
@ElDominio have you ever used any of the jumpers for any reason? can we remove all or replace with test vias if we ever need space on this PCB? if we want to make the PCB simpler?

ElDominio, 2022-11-20:
I didn't know what jumpers?? It has jumpers? Where?

Crank/Cam logic analyzer should be vias and not pads. Little holes i can solder pins to if necessary

rusefillc, 2022-11-21:
@ElDominio these jumpers between connectors and components

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

ElDominio, 2022-11-21:
fine to remove

rusefillc, 2023-03-15:
Some were removed to address mounting point issue. Technically theoretically sometimes having at least a via help, having complete jumper might help even more.

We can always remove individual ones if that helps with tracing or else. Replacing with a via keeps at least of some over-engineering.

rusefillc, 2023-03-16:
Actually closing to keep things simper

Closed 2023-03-16.

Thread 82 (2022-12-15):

Remove some of jumpers since two mounting points are grounding stuff

rusefillc, 2022-12-15:
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

rusefillc, 2022-12-15:
@ElDominio how come this is not an issue for you?

https://www.instagram.com/marsel_zx/ reports actual injector short

rusefillc, 2022-12-15:
i suggest removing the jumpers which are causing the issue and adding proper bolt mounting points

ElDominio, 2022-12-15:
Because i tape the bottom of the case because this happened on the old 4chans lol

rusefillc, 2022-12-15:
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

Nadezhda-n, 2023-01-26:
**_some_**
are there sizes?

rusefillc, 2023-01-26:
@Nadezhda-n let's remove 7 left and 7 right to behind with, sizes on Sunday

Nadezhda-n, 2023-01-26:
> @Nadezhda-n let's remove 7 left and 7 right to behind with, sizes on Sunday

wait for sunday

Nadezhda-n, 2023-01-30:
@rusefillc

rusefillc, 2023-01-30:
диаметр d=6.2mm
расстояние между центрами примернр 86.7мм

мы там не делаем крепёжных отверстий - просто делаем гладкую плату без голой меди

Nadezhda-n, 2023-01-31:
> диаметр d=6.2mm расстояние между центрами примернр 86.7мм
>
> мы там не делаем крепёжных отверстий - просто делаем гладкую плату без голой меди

а высота какая?
Плата ровно по центру корпуса?

rusefillc, 2023-01-31:
По центру

Closed 2023-01-31.

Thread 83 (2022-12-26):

Disable pull-up on CKP/CMP while staying in Hall mode

ElDominio, 2022-12-26:
For externally pulled-up hall sensors or using Max9926

For more context, I used a MAX9926 on a car that was having issues with the built-in VR module, and it worked fine for a while. Apparently now it's not pulling to ground properly, leading me to believe that disabling the 5V pullup will make the 9926 work correctly, since the 9926 seems to be outputting the correct signal when not connected to the ECU.

mck1117, 2022-12-27:
Set the pullup mode to VR. Controlling the pullup is the only thing it does.

ElDominio, 2022-12-27:
Does it not make it "look" at the VR Threshold?

mck1117, 2022-12-30:
nope, the VR input is separate to the MCU, so it doesn't matter what the VR conditioner circuit is doing.

mck1117, 2023-01-03:
nope, the digital input circuit is separate.

ElDominio, 2023-04-21:
Thank you for the clarification!

Closed 2023-04-21.

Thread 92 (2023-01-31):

Components are missing from alphax_4ch-f-components.png

rusefillc, 2023-01-31:
https://github.com/rusefi/alphax-4chan/blob/main/boards/alphax_4ch-f/board/misc/alphax_4ch-f-components.png does not have many components

rev E was better

is that a red flag of something broken somewhere on 4chan?

andreika-git, 2023-02-07:
It seems that gerber/alphax_4ch.wrl was exported incorrectly (the reason is unknown) - it didn't have most of the frame components... When I export it myself from the current alphax_4ch.kicad_pcb, the problem seems to be solved.

rusefillc, 2023-02-07:
@Qwerty-OFF @Nadezhda-n just FYI

let me close this one I guess, no need to re-generate anything version 'F' does not look critical

Closed 2023-02-07.

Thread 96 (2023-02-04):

5 and 6 cyl on main connector trick

rusefillc, 2023-02-04:
https://github.com/rusefi/alphax-4chan/issues/90 would allow 6 cylinder using aux connector
* we need through hole vias on aux 2x ignition traces to allow jumper wires
* (no action needed) let's make sure to keep at least some jumpers on less important pins like D4 FLEX knock opposite of https://github.com/rusefi/alphax-4chan/issues/76

This would allow 6 cylinder on main connectors with board mod.
* injectors 5 and 6 could be made from existing low sides by just removing diode

ElDominio, 2023-03-16:
Which existing GPIO could be used for injection?
if it could be any, like IDLE/IDLE2/NOS/VVT/VVT2, then I agree with what you said. My mind is on doing a 6x6 ETB engine with no VVT so losing VVT control loses me nothing

Qwerty-OFF, 2023-03-18:
IGN5-6 vias for ignition
IGN7-8 for VVT1-2 or INJ5-6 (need to remove D53, D54)
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

ElDominio, 2023-03-18:
Can this be done on older boards?

rusefillc, 2023-03-18:
> Can this be done on older boards?

probably no access to those MCU pads

Closed 2023-03-18.

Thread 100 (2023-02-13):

ETB behavior on 4chan

ElDominio, 2023-02-13:
So I have had differing experiences with Hellen-based hardware on hellen154 vs 4chan

On Hyundai 154, I can use autotune just fine, and the PID settings are usually
P = 0xx.xx
I = 0xxx.xx
D = 0.xxxx

On 4chan
P = 0x.xx (usually around 0.8-2)
I = 0xx.xx (usually around 10-15)
D = 0.0xxx (usually around 0.02-0.09)
Using autotune drives it too crazy, and usually overheats. Using settings by hand usually makes it works quite well.

rusefillc, 2023-02-13:
@Qwerty-OFF any ideas why would Hellen-based Hyundai 154 use ETB PID settings matching Proteus while Hellen-based would be pretty different, with PID auto-tune working on Proteus and Hyundai 154 but failing on 4chan?

mck1117, 2023-02-13:
What sort of capacitors does hyundai board use near the ETB chip? Ceramic or electrolytic?

Proteus -> electrolytic

4chan -> ceramic

rusefillc, 2023-02-13:
old hyundai https://raw.githubusercontent.com/wiki/rusefi/rusefi/Hardware/Hellen/hellen154hyundai-rev-b.jpg ceramic?

new hyundai I do not have any photo :( @ElDominio ?

8chan ceramic

Qwerty-OFF, 2023-02-27:
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

rusefillc, 2023-02-28:
@mck1117 adding electrolytic did not change anything :(

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

rusefillc, 2023-03-16:
@dron0gus says

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

rusefillc, 2023-03-16:
that did not help :(

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

rusefillc, 2023-03-16:
@mck1117 @andreika-git I am out of ideas. Sounds like we need an EE person to touch this? Would any sort of logs help do we even log useful stuff?

#109 created because why not

rusefillc, 2023-03-16:
https://github.com/rusefi/alphax-4chan/issues/110 another crazy one

mck1117, 2023-03-16:
I don't think there are any useful logs to have here that aren't an oscilloscope.

mck1117, 2023-03-16:
actually, can you take a maxed out TS rate log of auto calibrate both in the GOOD and BAD scenarios, for clear side-by-side comparison?

rusefillc, 2023-03-21:
@mck1117 poke about above good vs bad

andreika-git, 2023-03-24:
The 4chan log has "OBD_TPS1_Correlation" error, which means the problem is with TPS1 (hardware or wrong settings?) - that's why PID autotune fails.

mck1117, 2023-03-24:
bad left, good right

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

In the good case, it looks more sinusoidal, and in the bad case, it looks much steeper on opening than closing.

In the bad case there are also some weird "runt" cycles like this:
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

In the good case it's much more "stable"

mck1117, 2023-03-24:
> The 4chan log has "OBD_TPS1_Correlation" error, which means the problem is with TPS1 (hardware or wrong settings?) - that's why PID autotune fails.
>
> The OBD_TPS1_Correlation error appears when one of TPS sensors (TPS1 or TPS2) has an invalid signal. As a test, we can disable the TPS2 and try in 'ignoreSecond' mode.

That warning isn't active at the time autotune is running. That's not the problem.

mck1117, 2023-03-24:
> that's why PID autotune fails.

The logs show the firmware is doing fine, and doing the same thing in both cases. It also looks like something is electrically or mechanically wrong: see the weird TPS waveform on the "bad" log.

mck1117, 2023-03-24:
Wait, alphax 4chan is using pin C6 for PWM.

`stm32_common.cpp` says

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

But `mcuconf_common_f4_f7.h` says

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

4CHAN IS USING SOFTWARE PWM FOR ETB

mck1117, 2023-03-27:
> Damn that's a shameful issue :(

this should be a lesson for “electrical weirdness -> get out a scope and look at it instead of shooting in the dark for a month”

ElDominio, 2023-03-29:
@rusefillc was this tested before closing?

rusefillc, 2023-03-29:
> @rusefillc was this tested before closing?

yes. my bad not posting happy artifacts

and this justifies a new release actually!

ElDominio, 2023-03-29:
Tested today, way, way better results! :D

Closed 2023-03-27.

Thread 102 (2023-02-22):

rev F cap mod against hall digital noise [focus on C3 the one shared with VR][two modded boards in PR]

rusefillc, 2023-02-22:
How do we hand modify add caps for hall digital noise drama?

https://github.com/rusefi/alphax-4chan/issues/72

pins C3 and C7

actually it's mostly C3 which has issue. Is it same VR cap or different cap to improve mostly C3 digital hall input?

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

ElDominio, 2023-02-22:
Question, does changing to E5 help at all?

rusefillc, 2023-02-22:
Question: is there a difference between C3 and C7?

Qwerty-OFF, 2023-02-22:
C7 is traditional OpAmp input through Input module
C3 connected to VR discrete and Schmitt trigger
Try to add 1n capcitor:
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
And remove this:
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

rusefillc, 2023-02-23:
@timbelom please attempt two above mentioned mods on 4 chan rev E we have

* take 0805 cap marked 1n
* remove resistor as described

rusefillc, 2023-02-23:
@Qwerty-OFF посоветуй плиз куда кидать на землю конденсатор рядом с R22 тоже картинкой?

Qwerty-OFF, 2023-02-24:
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
Лучше использовать SMD

rusefillc, 2023-02-26:
@Qwerty-OFF my bad we have rev F not rev E, need same instructions for rev F with latest VR

rusefillc, 2023-02-26:
@Qwerty-OFF rev C does not have D57 is there a chance to fix rev C?

overall at the moment we have rev F and rev C to modify

rusefillc, 2023-02-27:
1nf
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

rusefillc, 2023-02-27:
Actually @Qwerty-OFF says to remove R753 to disconnect VR just for a test

rusefillc, 2023-02-27:
@ElDominio this board is on the way to you. Please test and share results :)

rusefillc, 2023-04-01:
@Qwerty-OFF we have positive test results! we need this mod on rev G

https://github.com/rusefi/rusefi/issues/5211#issuecomment-1493075254

Qwerty-OFF, 2023-04-02:
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

Closed 2023-04-02.

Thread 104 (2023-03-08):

rev F noise on digital-only C7 - [two boards modded differently with C200 variation]

rusefillc, 2023-03-08:
See white counter increases not with red line as expected

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

https://rusefi.com/online/view.php?msq=1416&dialog=triggerConfiguration cam uses C7

See also https://github.com/rusefi/alphax-4chan/issues/102

Qwerty-OFF, 2023-03-08:
Отличия от обычного входа CAM:
- подтяжка настраиваемая;
- подтяжка выполнена к +5VAS (TLS115), а не +5VA как обычно.

Давай попробуем сделать обычную подтяжку, для этого нужно отпаять R44 и поставить 4.7 кОм как на картинке
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

Следующий эксперимент с конденсатором C200, сейчас там 1 нФ, можно поставить 10 нФ и посмотреть что случится.

rusefillc, 2023-03-08:
@ElDominio I have mod instructions I need stuff to mod please :)

rusefillc, 2023-03-15:
* on two boards:
@Timbelom we have 5.6K through-hole resistors for sure, could be easier than 4.7K SMD
but we can try 4.7K maybe 1206 mounted vertically and a small wire?

* let's make one board with C200 replaced, one without C200 replaced

https://rusefi.com/docs/ibom/alphax_4ch-f-ibom.html
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

rusefillc, 2023-04-01:
@Qwerty-OFF we have positive test results! we need the mod on rev G. Looks like C200 part of the mod is not needed

https://github.com/rusefi/rusefi/issues/5211#issuecomment-1493075254

Qwerty-OFF, 2023-04-02:
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

rusefillc, 2023-04-02:
@andreika-git what are your thoughts? what change could have changed what why?

ElDominio, 2023-04-12:
@Qwerty-OFF question, would removing R44 and adding the 4.7k Resistor be an acceptable fix?

Qwerty-OFF, 2023-04-12:
@ElDominio yes
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

ElDominio, 2023-04-13:
But I also have to add a capacitor on D57 right?

rusefillc, 2023-04-13:
> D57

@ElDominio your comment seems to be first mentioning of D57 on this ticket? Please provide some context?

ElDominio, 2023-04-13:
I am trying to mod a RevC to work with 4G63

https://github.com/rusefi/alphax-4chan/issues/102#issuecomment-1446834216

Shows a capactior added to D57, but D57 does not exist on revC. I'm trying to figure out an equivalent position to place said capacitor to see if I can make it work.

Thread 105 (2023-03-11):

revG wishlist

ElDominio, 2023-03-11:
My requests for "next" revision of 4chan

-> all Hall/VR updates

* ~ETB overheating issues fix #100 [edit: software issue]~

* USB-C port instead of mini USB #78

* aux connector #90

* Built in baro onboard, so this menu is used (edit: you get this automatically same like 2chan already have it working since 10 minutes ago) https://github.com/rusefi/alphax-2chan/issues/87

* Default Tacho to 12v, add a removable component to change to 5V #38

ElDominio, 2023-03-15:
Move MAP location nearer to the middle of the board or close to connector, to evade damage during shipping

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

Like so
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

ElDominio, 2023-03-16:
#100 will not be fully implemented in G

Closed 2023-04-17.

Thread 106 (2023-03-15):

We need to move MAP sensor to a safer spot. Maybe add space for much more got glue/epoxy around MAP

rusefillc, 2023-03-15:
* We need space for much more got glue around MAP
* can we make a couple of 2mm vias on sides of MAP for hot glue to attach to holes?

Pictured rev F with too many components around allowing only for small amount of hot glue

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

ElDominio, 2023-03-15:
I think more glue is not the solution

Move MAP location nearer to the middle of the board or close to connector, to evade damage during shipping

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

Like so
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

mck1117, 2023-03-15:
> I think more glue is not the solution

Besides, no amount of glue will save you. The pins/PCB are stiffer than the glue, so any deflection will result in stress in the pins, not the glue. The pins will snap off, then the glue will bear the load only once that's happened. You need either a stiff urethane glue or epoxy, mechanical connection (ie, bolt), or move the sensor.

rusefillc, 2023-03-15:
@ElDominio says

Move MAP location nearer to the middle of the board or close to connector, to evade damage during shipping

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

Like so
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

rusefillc, 2023-03-15:
> move the sensor.

I agree, location on the edge seems to be the main issue

Qwerty-OFF, 2023-04-02:
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

rusefillc, 2023-04-02:
@Qwerty-OFF still on the edge :(

rusefillc, 2023-04-02:
@Qwerty-OFF can we move to

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

so that it's NOT on the edge of the board?

Qwerty-OFF, 2023-04-02:
![Uploading image.png…]()

Closed 2023-04-02.

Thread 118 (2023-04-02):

rev G 4g status

rusefillc, 2023-04-02:
Between firmware progress and hardware mods we got happy 4g running rev F!

* More than one EE is asking questions how does configurable VR/Hall even work https://github.com/rusefi/alphax-4chan/issues/117
* In light of above, we add safe capacitors and provision footprints for optional pull-ups see [102](https://github.com/rusefi/alphax-4chan/issues/102#issuecomment-1493395593)

rusefillc, 2023-04-17:
* usb-c took DFU firmware
* blue LED blinks

rusefillc, 2023-04-17:
* ETB moves with auto-calibrate works
* both TPS input sensors work
* injectors click in self-stim

rusefillc, 2023-04-18:
board No 2

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

rusefillc, 2023-04-18:
board No 3

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

rusefillc, 2023-04-18:
rev F just for reference. same exact firmware same exact testing apparatus

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

Qwerty-OFF, 2023-04-18:
PPS1:
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

rusefillc, 2023-04-18:
mux1,2 shows zero while R67 shows 2.6v

rusefillc, 2023-05-10:
@ElDominio says CAN bus works good on this 4chan rev G / mm-0.3

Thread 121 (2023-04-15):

4g experiments without touching VR pins

rusefillc, 2023-04-15:
We shall try to run 4g on rev F and rev G while NOT using C2,C3,E5,E6

meaning that we have C7 E3 E4

rusefillc, 2023-04-15:
@Qwerty-OFF E3 and E4 are they hall-compatible on either F or G?

rusefillc, 2023-04-15:
E3 and E4 have 100nF caps which would need to be removed or better changed to 1-10nF

ElDominio, 2023-04-15:
I have confirmed a simple fix on revC and revE

On revC, I did the same as was said by @Qwerty-OFF , adding 1nf caps to IN_CRANK and a 4.6k resistor to R7 jumper hole to R40 pad (removing R44 in the process)
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

still revC, added 1nf caps to IN_CRANK as shown here
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

and to D57 (on revF schematic) pad on R24
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

This allowed me to read RPM perfectly on 4G93 on a revC
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

ElDominio, 2023-04-15:
On revE, I **_ONLY_** added a 1nf cap from bottom pad of R24 to ground
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

And also reads perfectly
[perfect4reading4gonlyonecap.zip](https://github.com/rusefi/alphax-4chan/files/11240484/perfect4reading4gonlyonecap.zip)

This revE has stock R44 resistor, no resistors removed to disable VR, no external resistors, and no cap on IN_CRANK. Still works great.
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

ElDominio, 2023-04-16:
Fun fact: revE with 1nf cap ALSO works on VR car, specifically 24-1 cam speed Honda B20, with settings from unmodified ECU.

Closed 2023-12-05.

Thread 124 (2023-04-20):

test rev G Hall test default configuration with two resistors removed board number 0 C3+C4

rusefillc, 2023-04-20:
@ElDominio please confirm that you have a working heat gun
@ElDominio please do not use soldering iron to remove R4
@ElDominio please remove R4 using hot air and tweezers from back side. please place R4 into a little bag mark "R4"
@ElDominio please remove R23 not too far from R4. please place R23 into a little bag mark "R23"

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

capacitors stay default
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

@ElDominio need to run this board as hall on C3+C4

ElDominio, 2023-04-22:
Use C3 for CKP and C4 for CMP??

rusefillc, 2023-04-22:
@ElDominio yes that the request from what I see

rusefillc, 2023-04-28:
@ElDominio please provide a status update for this C3+C4

ElDominio, 2023-04-28:
C3+C4 works fine on easy Hall car Lancer with 4B11, tested on all boards.

Not tested on problematic hall 4G93 with split cam+crank

ElDominio, 2023-04-29:
Tried revving on board0 and board2, both worked fine @rusefillc

ElDominio, 2023-12-05:
RevG works with Hall/VR

Closed 2023-12-05.

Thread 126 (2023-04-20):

test rev G test VR configuration with two resistors removed board number 0, also boards 1 and 2

rusefillc, 2023-04-20:
Same physical unit as https://github.com/rusefi/alphax-4chan/issues/124

@ElDominio need to run this board as VR C2+C3

rusefillc, 2023-04-20:
board 1 has C17 removed

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

rusefillc, 2023-04-20:
board 2 has C20 added over default
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

ElDominio, 2023-04-26:
https://rusefi.com/online/view.php?log=1228

With resistors removed reads VR, without removing them, it did not read. Log is with resistors removed.

This car has run on revB/revC/revD so it seems to be a happy simple VR, pends testing on a car with more annoying VR

rusefillc, 2023-04-27:
@ElDominio
* fact 1: any rev board is useless in the as-soldered-on-factory resistor configuration
* fact 2: as of now I have not removed any resistor from any of the five rev G boards in existence
* conclusion: @ElDominio to remove R from any test board for any test

ElDominio, 2023-04-27:
board 2 log, r4 and r23 removed:
[revGtestVRver2.zip](https://github.com/rusefi/alphax-4chan/files/11347674/revGtestVRver2.zip)

board 1 log, r4 and r23 removed:
[revGtestVRver1.zip](https://github.com/rusefi/alphax-4chan/files/11347711/revGtestVRver1.zip)

board 0 log, r4 and r23 removed:
[revGtestVRver0.zip](https://github.com/rusefi/alphax-4chan/files/11347787/revGtestVRver0.zip)

all tests done on Toyota 1NZ 36-2 Crank, 4-1 cam, dual VR
tune file
[tuneforyaris.zip](https://github.com/rusefi/alphax-4chan/files/11347805/tuneforyaris.zip)

rusefillc, 2023-04-27:
@ElDominio tl,dr?

ElDominio, 2023-04-27:
all broken, can see sync failure on log

ElDominio, 2023-04-28:
This was tested on problematic VR from Toyota Yaris 1NZ

All boards could not rev past idle due to sync issues, the car works much better on revF

Easy VR from Honda B20 work fine on board 0

Qwerty-OFF, 2023-04-28:
Please remove R22, R35, R1126, R1135 on board 1 (without C17, C20) and check VR C2+C3 again

rusefillc, 2023-04-28:
@ElDominio https://rusefi.com/docs/ibom/alphax_4ch-g-ibom.html

ElDominio, 2023-04-29:
I think it is worse now
[moddedwithoutalotofresistorsboardv1revG.zip](https://github.com/rusefi/alphax-4chan/files/11360218/moddedwithoutalotofresistorsboardv1revG.zip)

rusefillc, 2023-04-29:
@ElDominio please add a photo with all mods?

ElDominio, 2023-04-29:
![IMG_20230429_192301.jpg](https://user-im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

17-02864297-7550-47fe-8a32-603438daf84f.jpg)

![Uploading IMG_20230429_192246.jpg …]()

rusefillc, 2023-04-29:
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

ElDominio, 2023-07-23:
Can this and revG tickets be closed yet? I don't see why not?

Closed 2023-07-23.

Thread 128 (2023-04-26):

VR VVT issues

ElDominio, 2023-04-26:
In this log i change VR threshold for cam input, and the cam angle changes, I don't think this is right, started at 0.3 and kept adding .1 until i got to 1

https://rusefi.com/online/view.php?log=1229

you can see VVT angle change as i change VR threshold

mck1117, 2023-04-26:
Is this an ECU with fixed capacitors?

ElDominio, 2023-04-26:
Yep, revF

mck1117, 2023-04-26:
where's the tune

mck1117, 2023-04-26:
also, have a trigger scope?

ElDominio, 2023-04-26:
Tune is attached to log on rusefi online ;_;
https://rusefi.com/online/view.php?msq=1459 here's the link anyways

no trigger scope cause I don't have the car, should have it on Thursday

ElDominio, 2023-04-27:
[revF oscope log.zip](https://github.com/rusefi/alphax-4chan/files/11347615/revF.oscope.log.zip)

i managed to stall it mid log

mck1117, 2023-04-28:
Trigger scope looks fine. Your triggers are configured correctly for what I see on the scope.

Thresholds also look fine, you can set them pretty high once the engine is running. Not sure why you're seeing timing move with threshold level.

Aside: why does the VVT position move with RPM?

ElDominio, 2023-04-28:
Because I targetted different positions with RPM? i guess lol

I set inverted to True and it seems MUCH more stable, as in useable. I'll close this for now since it seems to be okay

Closed 2023-04-28.

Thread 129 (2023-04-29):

VR+hall quesiton and suggested fix idea

ElDominio, 2023-04-29:
revF VR+Hall circuit seems to work quite well, only needing a 1nf cap Net-D57 to GND as shown https://github.com/rusefi/alphax-4chan/issues/121#issuecomment-1509942883 here.

Why did the revG circuit change so much? Can we just do revF VR circuit + the previously mentioned capacitor? Removing/adding said capacitor sounds much less painful than the current state

rusefillc, 2023-04-29:
Really question is "is it possible to adjust current rev G pieces to match rev F 100%?"

Qwerty-OFF, 2023-04-29:
For F ~100%
Remove C135, C141, C142 (because in MM the capacitance on "IN_Dx" lines is 2 x 1nf)
Remove C17, C20, C21
https://github.com/rusefi/alphax-4chan/issues/121#issuecomment-1509942883 not needed (already done)
Remove R4, R39
Install R21, R23 if they are removed
This covers everything related to the lines IN_CRANK+, IN_CRANK-, IN_CAM_VR+, IN_CAM_VR-, IN_CAM_HALL, and IN_2STEP.

ElDominio, 2023-04-29:
How about RevF on IN_CRANK+/- and IN_CAM_VR+/-? Without changing IN CAM HALL and IN 2STEP?

ElDominio, 2023-04-29:
> For F ~100% Remove C135, C141, C142 (because in MM the capacitance on "IN_Dx" lines is 2 x 1nf) Remove C17, C20, C21 [#121 (comment)](https://github.com/rusefi/alphax-4chan/issues/121#issuecomment-1509942883) not needed (already done) Remove R4, R39 Install R21, R23 if they are removed This covers everything related to the lines IN_CRANK+, IN_CRANK-, IN_CAM_VR+, IN_CAM_VR-, IN_CAM_HALL, and IN_2STEP.

On what board? V0, V1, V2?

rusefillc, 2023-04-30:
Your choice?

Reminder that v0 has c17 as from factory and one of v1/v2 has c17 removed and moved on another board as C20. All other mods you've done yourself.

rusefillc, 2023-04-30:
https://rusefi.com/docs/ibom/alphax_4ch-g-ibom.html is helpful to locate C17 and C20

ElDominio, 2023-04-30:
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

Question, with the current setup, can IN_2STEP be used as either a Hall input _or_ 2step input? Because I like that and I tested C4 already and it worked

>  your choice?\n\nReminder that v0 has c17 as from factory and one of v1/v2 has c17 removed and moved on another board as C20. All other mods you've done yourself.

I will test this hopefully tomorrow.

rusefillc, 2023-04-30:
@ElDominio  what is 2step input? just a mechanical button. Hall still has pull-up I assume (you can check with a digital multimeter by checking for disconnected wire) thus yes, same hall or just button

ElDominio, 2023-04-30:
> @ElDominio what is 2step input? just a mechanical button? Hall still has pull-up I assume (you can check with a digital multimeter by checking for disconnected wire) thus yes, same hall or just button

Yep, a mechanical button that pulls to ground.
So it would be best to not modify that input and keep it as is, then have ONLY the two VR circuits as they are in revF

rusefillc, 2023-04-30:
> So it would be best to not modify

I have no idea what that means.

a) are you requesting we undo rev G and start from rev F again?
b) are you requesting something else? what is the ask specifically?

ElDominio, 2023-04-30:
When I test I will have a more concrete request, so no action until then

My current request is:
How do i modify IN_CRANK+/- and IN_CAM+/- without touching IN_2STEP in revG board2?

rusefillc, 2023-04-30:
@Qwerty-OFF says

Something still needs to be done with 2step, either as in https://github.com/rusefi/alphax-4chan/issues/129#issuecomment-1528831105 to get 100% rev. f, or install R39 and remove R23 to get a better chance for the HALL or button on the 2_STEP line to work correctly

ElDominio, 2023-05-01:
> For F ~100% Remove C135, C141, C142 (because in MM the capacitance on "IN_Dx" lines is 2 x 1nf) Remove C17, C20, C21 [#121 (comment)](https://github.com/rusefi/alphax-4chan/issues/121#issuecomment-1509942883) not needed (already done) Remove R4, R39 Install R21, R23 if they are removed This covers everything related to the lines IN_CRANK+, IN_CRANK-, IN_CAM_VR+, IN_CAM_VR-, IN_CAM_HALL, and IN_2STEP.

what about R1126 and R1135?

ElDominio, 2023-05-01:
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

ElDominio, 2023-05-02:
@Qwerty-OFF was I expected to have R22/R33/etc removed or not? All the 1206 resistors?

Qwerty-OFF, 2023-05-02:
R22/R33/etc R1206 should be installed for rev.f comatibility. They are for the IN_CRANK+, IN_CRANK- and IN_CAM_VR+ use as hall sensor input circuits.

Qwerty-OFF, 2023-05-02:
R1126 and R1135 is missing designators on rev. f and rev. g boards (or not?)

ElDominio, 2023-05-02:
Picture on comment 1530226901 updated to explain what was done

[fullymoddedtorevFcomment1528831105ticket129.zip](https://github.com/rusefi/alphax-4chan/files/11378084/fullymoddedtorevFcomment1528831105ticket129.zip)

The car does not seem happy, but it currently runs quite well on a revF (actual revF hardware)

rusefillc, 2023-05-02:
@Qwerty-OFF seems like "100% rev F compatible" somehow is not 100% rev F compatible :(

Qwerty-OFF, 2023-05-02:
I'll think tomorrow about what other differences there are. Is the problem with pins C2+C3?

Qwerty-OFF, 2023-05-02:
I'll think tomorrow about what other differences there are. Is the problem with pins C2+C3?

ElDominio, 2023-05-02:
> I'll think tomorrow about what other differences there are. Is the problem with pins C2+C3?

Good observation, this car uses dual VR C2+c3 AND E5+E6

If E5+E6 is not revF, cam will not read correctly

Qwerty-OFF, 2023-05-03:
CAM VR differences seem to be fixed by https://github.com/rusefi/alphax-4chan/issues/129#issuecomment-1528831105
Remove C211, C216 (or replace with 1nF if possible)
Ensure that R753_2 is not removed from the board

ElDominio, 2023-05-05:
@Qwerty-OFF VR on Toyota 1NZ 36-2  seems to have improved significantly,
car runs the same as revF (removed c211, c216 replaced with 1nf)
R753_2 was present

logs
regular TS log of engine running:
[crankingrevGmay4.zip](https://github.com/rusefi/alphax-4chan/files/11409612/crankingrevGmay4.zip)

oscope:
[triggeroscoperevgmay4.zip](https://github.com/rusefi/alphax-4chan/files/11409614/triggeroscoperevgmay4.zip)

ref @rusefillc

ElDominio, 2023-05-05:
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

ElDominio, 2023-05-05:
I have idled and revved for about 15 minutos now, seems okay

ElDominio, 2023-05-07:
https://docs.google.com/spreadsheets/d/1M2a5KM3GcPGP_YP6OwbdvqBgPWTfrZ21yheXTK44Okg/edit?usp=sharing

Here is a sheet with all current board states, only truly known is board1, will fill out others later

ElDominio, 2023-05-12:
@Qwerty-OFF  i have updated the spreadsheet, and will have the test car for about three more days. Is there any more tests that need to be done?

Closed 2023-07-23.

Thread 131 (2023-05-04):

ibom: cannot click on passives above D203

rusefillc, 2023-05-04:
https://rusefi.com/docs/ibom/alphax_4ch-g-ibom.html

Good:
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

Bad:
cannot do this with similar components right above D203

andreika-git, 2023-05-10:
Cannot reproduce (works on both Chrome and Firefox):

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

rusefillc, 2023-05-10:
step 1: click https://rusefi.com/docs/ibom/alphax_4ch-g-ibom.html
step 2: do NOT click "FB" mode
step 3: click above D204 happy
step 3: click above D203 unhappy

andreika-git, 2023-05-10:
Some of 10k/0402 resistors have wrong part numbers (510k instead of 10k). That's why they were duplicated in the BOM - and it could possibly cause this bug of partial selection (those resistors above D203 are 10k). Maybe we should fix the mega-mcu BOM first and then continue to test the 4chan iBom.

rusefillc, 2023-05-10:
@andreika-git стоит ли нам защищаться от некорректных данных, или непросто?

andreika-git, 2023-05-11:
> @andreika-git стоит ли нам защищаться от некорректных данных, или непросто?

https://github.com/andreika-git/hellen-one/issues/293

rusefillc, 2023-05-15:
@Qwerty-OFF please mention relevant 4chan changes just to have a changelog

Qwerty-OFF, 2023-05-15:
Вот у этих компонентов была неправильный PN. Вместо 10k стали 510k.
"10k","R102, R108, R109, R121, R127, R128, R141, R142, R232, R233, R234","R0402","C11616"
В ревизии h все кроме R232 получили правильный PN "C25744". R232 стал DNP (была ошибка в rev. g - https://github.com/rusefi/alphax-4chan/issues/137)

rusefillc, 2023-05-16:
@Qwerty-OFF @andreika-git this ticket is about ibom glitch.

If we have something important going on with five rev G boards in the wild please improve the messaging and making it more obvious what is the level of risk where etc.

andreika-git, 2023-05-16:
https://github.com/andreika-git/hellen-one/issues/295

andreika-git, 2023-05-18:
Fixed by fixing https://github.com/andreika-git/hellen-one/issues/295

Closed 2023-05-18.

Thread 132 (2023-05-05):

VVT output F2 not working on RevG

ElDominio, 2023-05-05:
VVT seems to not work on revG, testing on Yaris

log: https://rusefi.com/online/view.php?log=1232
tune is linked to log on rusefi online

possible culprit sames as revG PPS?

rusefillc, 2023-05-06:
rev G
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

rusefillc, 2023-05-06:
rev F
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

rusefillc, 2023-05-06:
@ElDominio yes VVT1 and VVT2 pinout has changed on rev G, now adding "F2 - VVT#1 rev G" and "F4 - VVT#2 rev G" pins

ElDominio, 2023-05-06:
Is there a way to catch any other pins like these?

rusefillc, 2023-05-06:
@ElDominio yes, just go over all pins in the schematics

rusefillc, 2023-05-07:
Also https://rusefi.com/docs/pinouts/hellen/alphax-4chan/ progress has helped since it at least detects pin overlap.

Legacy VVT pins have funny names in latest firmware.

ElDominio, 2023-08-25:
This seems to still be broken; did it break when removing old compatibility?

rusefillc, 2023-08-25:
@ElDominio please clarify why closed?

ElDominio, 2023-08-25:
Did not know if a new ticket was better, asking for processor pins.

rusefillc, 2023-08-25:
https://github.com/rusefi/alphax-4chan/issues/159 not better

rusefillc, 2023-12-03:
@ElDominio too many things bundled together here - random vehicle etc etc

when one suspects a hardware problem on the board we have to start by testing physical output on a bench. clicking a known good test injector using "injector bench" button seems to be the most reliable way

i have a rev G board which passes stim QC testing on both vvt and idle outputs that confirm that firmware is capable of toggling output wire

```
 * Board detected: 4chan rev index 1
                      numOutputs 8
               Setting ADDR 0
               sending line=1 value=1
                      ADC says HIGH 1@0 3.080v
               sending line=1 value=0
                      ADC says LOW 1@1 0.002v
               sending line=1 value=1
               sending line=1 value=0
0/16 A8 - Injector 1 GOOD channel 1
               Setting ADDR 1
               sending line=2 value=1
                      ADC says HIGH 2@0 3.080v
               sending line=2 value=0
                      ADC says LOW 2@1 0.002v
               sending line=2 value=1
               sending line=2 value=0
1/16 B8 - Injector 2 GOOD channel 2
               Setting ADDR 2
               sending line=3 value=1
                      ADC says HIGH 3@0 3.080v
               sending line=3 value=0
                      ADC says LOW 3@1 0.002v
               sending line=3 value=1
               sending line=3 value=0
2/16 D1 - Injector 3 GOOD channel 3
               Setting ADDR 3
               sending line=4 value=1
                      ADC says HIGH 4@0 3.080v
               sending line=4 value=0
                      ADC says LOW 4@1 0.002v
               sending line=4 value=1
               sending line=4 value=0
3/16 E1 - Injector 4 GOOD channel 4
               Setting ADDR 4
               sending line=5 value=1
                      ADC says HIGH 5@0 1.399v
               sending line=5 value=0
                      ADC says LOW 5@1 0.001v
               sending line=5 value=1
               sending line=5 value=0
4/16 F2 - VVT#1 rev G GOOD channel 5
               Setting ADDR 5
               sending line=6 value=1
                      ADC says HIGH 6@0 1.604v
               sending line=6 value=0
                      ADC says LOW 6@1 0.002v
               sending line=6 value=1
               sending line=6 value=0
5/16 F4 - VVT#2 rev G GOOD channel 6
               Setting ADDR 6
               sending line=7 value=1
                      ADC says HIGH 7@0 1.688v
               sending line=7 value=0
                      ADC says LOW 7@1 0.002v
               sending line=7 value=1
               sending line=7 value=0
6/16 F1 - Idle2 GOOD channel 7
               Setting ADDR 7
               sending line=8 value=1
                      ADC says HIGH 8@0 1.720v
               sending line=8 value=0
                      ADC says LOW 8@1 0.001v
               sending line=8 value=1
               sending line=8 value=0
7/16 C8 - Idle GOOD channel 8
```

Closed 2023-12-03.

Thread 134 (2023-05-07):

rev G SD card

rusefillc, 2023-05-07:
With rev G moved to mega-module we need conditional SD card initialization to have SD card working on both legacy and newer 4chan boards

https://github.com/rusefi/rusefi/commit/599a97b3aac7eb9b8e550e36fc8bc732f7c63fde is trying to help

rusefillc, 2023-05-07:
```
2023-05-07_11_18_13_779: EngineState: pin PA1: AFR
2023-05-07_11_18_13_780: EngineState: pin PA2: BarometricPressure
2023-05-07_11_18_13_780: EngineState: pin PA3: AcceleratorPedalPrimary
2023-05-07_11_18_13_780: EngineState: pin PA4: Tps1Primary
2023-05-07_11_18_13_781: EngineState: pin PA5: BatteryVoltage
2023-05-07_11_18_13_782: EngineState: pin PA6: Trigger #2
2023-05-07_11_18_13_782: EngineState: pin PA8: Fuel pump Relay
2023-05-07_11_18_13_785: EngineState: pin PA9: a-crank-p
2023-05-07_11_18_13_785: EngineState: pin PA11: USB DM
2023-05-07_11_18_13_785: EngineState: pin PA12: USB DP
2023-05-07_11_18_13_787: EngineState: pin PB0: Tps1Secondary
2023-05-07_11_18_13_787: EngineState: pin PB1: Trigger #1
2023-05-07_11_18_13_788: EngineState: pin PB3: SPI clock
2023-05-07_11_18_13_789: EngineState: pin PB4: SPI master in
2023-05-07_11_18_13_790: EngineState: pin PB5: SPI master out
2023-05-07_11_18_13_790: EngineState: pin PB6: SD CS
2023-05-07_11_18_13_792: EngineState: pin PC1: MapSlow
2023-05-07_11_18_13_793: EngineState: pin PC2: Clt
2023-05-07_11_18_13_794: EngineState: pin PC3: Iat
2023-05-07_11_18_13_794: EngineState: pin PC4: AcceleratorPedalSecondary
2023-05-07_11_18_13_795: EngineState: pin PC6: ETB Enable
2023-05-07_11_18_13_795: EngineState: pin PC7: Boost
2023-05-07_11_18_13_795: EngineState: pin PC8: VR PWM
2023-05-07_11_18_13_795: EngineState: pin PC13: Coil 1
2023-05-07_11_18_13_796: EngineState: pin PD0: CAN RX
2023-05-07_11_18_13_797: EngineState: pin PD1: CAN TX
2023-05-07_11_18_13_798: EngineState: pin PD2: a-crank-n
2023-05-07_11_18_13_799: EngineState: pin PD3: a-tach
2023-05-07_11_18_13_800: EngineState: pin PD4: ETB Dir 1
2023-05-07_11_18_13_801: EngineState: pin PD5: Primary UART RX
2023-05-07_11_18_13_803: EngineState: pin PD6: Primary UART TX
2023-05-07_11_18_13_803: EngineState: pin PD7: ETB disable
2023-05-07_11_18_13_803: EngineState: pin PD9: a-d2
2023-05-07_11_18_13_803: EngineState: pin PD10: Injector 4
2023-05-07_11_18_13_803: EngineState: pin PD11: Injector 3
2023-05-07_11_18_13_803: EngineState: pin PD12: Vvt Output#2
2023-05-07_11_18_13_803: EngineState: pin PD14: VR PWM
2023-05-07_11_18_13_804: EngineState: pin PD15: Vvt Output#1
2023-05-07_11_18_13_804: EngineState: pin PE3: Coil 4
2023-05-07_11_18_13_804: EngineState: pin PE4: Coil 3
2023-05-07_11_18_13_804: EngineState: pin PE5: Coil 2
2023-05-07_11_18_13_804: EngineState: pin PE7: led: comm status
2023-05-07_11_18_13_804: EngineState: pin PE8: led: warning status
2023-05-07_11_18_13_804: EngineState: pin PE10: mm-EN
2023-05-07_11_18_13_804: EngineState: pin PE13: clutch down switch
2023-05-07_11_18_13_805: EngineState: pin PF2: ADC Mux
2023-05-07_11_18_13_805: EngineState: pin PF8: trg ch2
2023-05-07_11_18_13_805: EngineState: pin PF10: trg ch1
2023-05-07_11_18_13_805: EngineState: pin PF12: a-d3
2023-05-07_11_18_13_805: EngineState: pin PF13: a-d4
2023-05-07_11_18_13_805: EngineState: pin PF14: a-d5
2023-05-07_11_18_13_805: EngineState: pin PG0: led: CRITICAL status
2023-05-07_11_18_13_806: EngineState: pin PG1: led: running status
2023-05-07_11_18_13_807: EngineState: pin PG2: Fan Relay
2023-05-07_11_18_13_808: EngineState: pin PG3: a-2step
2023-05-07_11_18_13_810: EngineState: pin PG4: a-cam
2023-05-07_11_18_13_811: EngineState: pin PG5: a-temp
2023-05-07_11_18_13_812: EngineState: pin PG6: tachOut
2023-05-07_11_18_13_813: EngineState: pin PG7: Injector 1
2023-05-07_11_18_13_814: EngineState: pin PG8: Injector 2
2023-05-07_11_18_13_815: EngineState: pin PG12: Main Relay
2023-05-07_11_18_13_815: EngineState: pin PG13: a-cam-vr
2023-05-07_11_18_13_816: EngineState: pin PG14: a-EN
2023-05-07_11_18_13_817: EngineState: Total pins used: 63
2023-05-07_11_18_13_818: EngineState: confirmation_pins:4
```

```
2023-05-07_11_20_44_913: EngineState: MMC CS PB6
2023-05-07_11_20_44_913: EngineState: SD enabled=Yes status=MMC_CONNECT_FAILED
2023-05-07_11_20_44_913: EngineState: SD SPI_DEVICE_1 mosi=PB5
2023-05-07_11_20_44_913: EngineState: SD SPI_DEVICE_1 miso=PB4
2023-05-07_11_20_44_914: EngineState: SD SPI_DEVICE_1 sck=PB3
2023-05-07_11_20_44_914: EngineState: confirmation_sdinfo:6
```

rusefillc, 2023-05-07:
``hellenBoardId=203``

rusefillc, 2023-05-07:
fix
```
2023-05-07_11_56_57_873: EngineState: pin PB7: mm-CS2
```

```
2023-05-07_11_57_38_084: EngineState: MMC CS PB6
2023-05-07_11_57_38_084: EngineState: SD enabled=Yes status=MSD
2023-05-07_11_57_38_084: EngineState: SD SPI_DEVICE_1 mosi=PB5
2023-05-07_11_57_38_085: EngineState: SD SPI_DEVICE_1 miso=PB4
2023-05-07_11_57_38_085: EngineState: SD SPI_DEVICE_1 sck=PB3
2023-05-07_11_57_38_085: EngineState: confirmation_sdinfo:6
```

Closed 2023-05-07.

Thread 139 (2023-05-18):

Fix BOM (see warnings.log)

andreika-git, 2023-05-18:
Current revision (rev.I) generates some warnings:

```
* Warning! Footprint mismatch for the part #C269114: R1206 != SMD1206
* Warning! Identical parts C753,C754,C759,C100,C101,C105,C108,C109,C110,C111,C112,C113,C118,C119,C120,C121,C122,C124,C126,C127,C128,C129,C130,C134,C147,C170,C175,C180,C185,C190,C195,C204,C205,C206,C207,C217,C218,C220,C221,C222,C230,C231,C232,C233,C270,C275,C280,C285,C753_2,C754_2,C759_2 and C411,C413,C420,C470 (100n_C0402) have different partnumbers: C1525 and C307331
* Warning! Identical parts VD100,VD101,VD102,VD103 and D18,D19,D23 (BAT54S_SOT-23) have different partnumbers: C47546 and C408389
* Warning! Identical parts R125,R170,R171,R175,R176,R180,R181,R185,R186,R190,R191,R196,R197 and R1,R2,R5,R50,R51,R200,R209,R218,R227,R236,R245,R257 (4.7k_R0603-4) have different partnumbers: C66697 and C1980
* Warning! Identical parts R232,R233,R234 and R421,R424,R425,R757,R762,R763,R767,R768,R102,R108,R109,R121,R127,R128,R141,R142,R757_2,R762_2,R763_2,R767_2,R768_2 (10k_R0402) have different partnumbers: C11616 and C25744
```

Qwerty-OFF, 2023-05-18:
`Warning! Identical parts C753,C754,C759,C100,C101,C105,C108,C109,C110,C111,C112,C113,C118,C119,C120,C121,C122,C124,C126,C127,C128,C129,C130,C134,C147,C170,C175,C180,C185,C190,C195,C204,C205,C206,C207,C217,C218,C220,C221,C222,C230,C231,C232,C233,C270,C275,C280,C285,C753_2,C754_2,C759_2 and C411,C413,C420,C470 (100n_C0402) have different partnumbers: C1525 and C307331`

16V and 50V. Do we need different values for the Value field for such situations? Or use 50V everywhere? The price difference is about $0.3 per board.

`Warning! Identical parts VD100,VD101,VD102,VD103 and D18,D19,D23 (BAT54S_SOT-23) have different partnumbers: C47546 and C408389`

Fixed, similar parts, but different PN

`Warning! Identical parts R125,R170,R171,R175,R176,R180,R181,R185,R186,R190,R191,R196,R197 and R1,R2,R5,R50,R51,R200,R209,R218,R227,R236,R245,R257 (4.7k_R0603-4) have different partnumbers: C66697 and C1980`

5% and 1%. Fixed, now 1% everywhere

`Warning! Identical parts R232,R233,R234 and R421,R424,R425,R757,R762,R763,R767,R768,R102,R108,R109,R121,R127,R128,R141,R142,R757_2,R762_2,R763_2,R767_2,R768_2 (10k_R0402) have different partnumbers: C11616 and C25744`

Wrong PN for 10k in pullups.csv. Fixed

andreika-git, 2023-05-19:
> 16V and 50V. Do we need different values for the Value field for such situations? Or use 50V everywhere? The price difference is about $0.3 per board.

I vote for using 50V caps everywhere, because "12V" can be actually 14.8V (or even higher) which is too close to 16V...

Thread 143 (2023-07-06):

RevH Tacho output not working but changing between 5v/12v

ElDominio, 2023-07-06:
As stated, tacho does not work (no wave on oscope) but switching voltage in Fancy Hardware DOES change voltage.

Was a pin changed from revF to revH to drive the tacho?

rusefillc, 2023-07-14:
@ElDominio do you know resistance of that tach? Do you want me to get same real tachometer for tests?

ElDominio, 2023-07-14:
Test 1: tacho output set to 12v and pin A4

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

Test 2: tacho output using Aux10, internal 4chan

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

ElDominio, 2023-07-20:
Are scopes useful? Any update?

Closed 2023-07-29.

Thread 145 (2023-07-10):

P1 adjust main connector DO NOT CLOSE UNTIL LIBRARY CHANGED

rusefillc, 2023-07-10:
the hole pitch is 4.2/4.2/3.33mm, GERBER is 4.0/4.0/3.5mm

@Qwerty-OFF мы можем сделать что-то универсальное? немного овальные отверстия может быть? я что-то могу намерять своими разъёмами полезного?

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

Qwerty-OFF, 2023-07-10:
Если ты сможешь измерить с точностью 0.2мм, давай узнаем сколько там должно быть на самом деле

rusefillc, 2023-07-11:
[delphi_12042017_HCCPHPE24BKA90F-1224853.pdf](https://github.com/rusefi/alphax-4chan/files/12010120/delphi_12042017_HCCPHPE24BKA90F-1224853.pdf)

rusefillc, 2023-07-11:
ха, внезапно он существует официальный и новый и в принципе его можно в JLC заказать

Qwerty-OFF, 2023-07-11:
Сделал отверстия увеличенного размера для совпадения со старым вариантом и с тем что в документе.
@rusefillc Если все будет хорошо, заставь меня переложить модифицированный компонент в kicad6-libraries для дальнейшего использования

Qwerty-OFF, 2023-10-16:
TODO использовать в следующей ревизии символ из библиотеки

rusefillc, 2023-10-17:
https://github.com/rusefi/kicad6-libraries/commit/ccd7bead220f3861fc2b8eb6ab7e77dbb559d2a7

Closed 2023-12-09.

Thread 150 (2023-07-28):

Pin E2 Out NOS not working, correct processor pin? On revH

ElDominio, 2023-07-28:
I am using for AC relay control. I can see 12v from the relay when blower is on, but no software change drives the transistor. Is the processor pin correct?

rusefillc, 2023-07-28:
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

rusefillc, 2023-07-28:
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

rusefillc, 2023-07-28:
https://github.com/rusefi/rusefi/blob/162507ca0d06c26ecb05785335fa6bf32e597dbb/firmware/config/boards/hellen/alphax-4chan/connectors/main.yaml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

@Qwerty-OFF please confirm?

Qwerty-OFF, 2023-07-28:
Yes that's right

rusefillc, 2023-07-28:
@ElDominio we do not see any problems here need more info

rusefillc, 2023-08-02:
@ElDominio any details?

Closed 2023-08-09.

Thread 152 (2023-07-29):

maybe it kind of works [was Split packages for legacy 4chan (revF and before) and current 4chan (revG and above)]

ElDominio, 2023-07-29:
I updated a revF today and lost tach, which I suppose is because I had asked for #146

Would it not be best to have two seperate packages for them? To avoid pinout problems?

My current fix:
Will downgrade to june release

rusefillc, 2023-07-29:
https://github.com/rusefi/rusefi/commit/baaec6ff328077994a03cd216287685844d2a026

so we have two options for D3 now

"D3 - Digital In 2 legacy up to rev F"
"D3 - Digital In 2 (A4 tach out up to rev F)"

ElDominio, 2023-07-29:
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

I can't choose tach output in outputs menu telling it that it is a revF

rusefillc, 2023-07-29:
Ohh stuff was not generating due to issue around https://github.com/rusefi/rusefi/pull/5412

rusefillc, 2023-07-29:
@ElDominio pinout and stuff is more properly generated now

https://rusefi.com/docs/pinouts/hellen/alphax-4chan/?pin=D3

ElDominio, 2023-12-05:
Pinouts between pre-RevG and RevG+ change, and my solution is to keep a July (20230705) firmware for when RevF downwards ECUs show up at my shop.

Closed 2023-12-05.

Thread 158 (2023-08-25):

ETB error? Calibrates ok but fails to control instantly

ElDominio, 2023-08-25:
4chan RevH F7

I do calibration procedure, everything works as normal but fails after calibrating (position is 0 and etb motor is disabled)

FIrmware 20230708

log: https://rusefi.com/online/view.php?log=1275

ElDominio, 2023-08-25:
I "fixed" it by setting it to Ford TPS mode at 50%

Closed 2023-12-05.

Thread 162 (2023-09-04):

document ETB capacitors

rusefillc, 2023-09-04:
https://github.com/rusefi/alphax-4chan/issues/110 has added electrolytic while not removing ceramic capacitors

we have never removed electrolytic from BOM even while https://github.com/rusefi/alphax-4chan/issues/110 was implying only footprint for custom board manual modification

At the moment all recent 4chan were fabricated with both sets? Is that a bug or a feature? Let's add text comment on the ETB page.

rusefillc, 2023-09-04:
let's move optional (?) electrolytic capacitor from the reusable reusable page to 4chan main page and mention that it technically is not needed

Qwerty-OFF, 2023-09-04:
Done, electrolytic capacitor is now DNP
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

Closed 2023-09-04.

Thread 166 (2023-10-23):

Make Battery Voltage read from A2 (main relay)  instead of F7

ElDominio, 2023-10-23:
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
Pictured: Key input has 11.3v when battery has 12.1v

Using key input as battery voltage is incorrect since we base our Dwell and Injection dead time corrections off battery voltage, we should read from the same source. On most cars, key-on is usually a bit smaller voltage than main relay, but sometimes even 1v off.

rusefillc, 2023-10-25:
@ElDominio this is harder than just a hardware change. At the moment we engage main relay when we sense voltage on ignition key.

if we only make the hardware change we would have to adjust 4chan settings to ALWAYS engage main relay which I assume is not desired.

For 4chan to read voltage from main relay we would need to ADD analog input not just MOVE.

@ElDominio looks like we would have to reuse one of aux analog inputs for main relay voltage. I suggest https://rusefi.com/docs/pinouts/hellen/alphax-4chan/?pin=X3

@ElDominio please confirm that we repurpose X3 analog input for main relay input

ElDominio, 2023-10-25:
Can we not sense ignition ON voltage with a digital pin, then use analog to read voltage from A2?

ElDominio, 2023-11-04:
I made a circuit to do this in one of my boards, if you want i can post it here (external main relay control)

ElDominio, 2023-11-09:
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

just in case

rusefillc, 2023-12-05:
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

rusefillc, 2023-12-07:
@ElDominio I do not have brain capacity to deal with this until January.

Do you want "rev-i" without this ticket in Dec or with it in January?

ElDominio, 2023-12-07:
With it in January

rusefillc, 2023-12-10:
```
#if EFI_MAIN_RELAY_CONTROL
	hasIgnitionVoltage = Sensor::getOrZero(SensorType::BatteryVoltage) > 5;
```

rusefillc, 2023-12-10:
Let me remove R53 to test https://github.com/rusefi/rusefi/commit/3b88f847e0370de6afc359f88c7c315cf695689c

open question what pin to use for ignitionKeyDigitalPin

rusefillc, 2023-12-10:
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

Qwerty-OFF, 2023-12-10:
Схема не подойдет для вариантов где всегда (на заглушенной машине) есть напряжение на нашем vign входе, будет разряжать аккумулятор. Также измерение напряжения главного реле через резисторный делитель тоже будет расходовать заряд батареи. Для автомобилей у которых питание always hot и запуск по can wakeup надо придумать что-то лучше.

rusefillc, 2023-12-12:
устал я от этой темы, я уже согласен на второй аналоговых вход

а можем ли мы сделать AV из AT1 например удалением резистора?

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

Qwerty-OFF, 2023-12-12:
Да, можно сделать av через replace

rusefillc, 2023-12-12:
@Qwerty-OFF давай заведём main relay +12v на AT1 с делителем

Closed 2023-12-16.

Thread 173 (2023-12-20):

Can High side Outputs drive VVT solenoids

ElDominio, 2023-12-20:
Ask question states, can high side output drive a VVT solenoid that has one side wired to ground?

rusefillc, 2023-12-20:
@ElDominio please provide context what pins are you asking about? ignition control I am sure is too weak

ElDominio, 2023-12-20:
Internal High1 and High2, the ones on the molex microfit

Qwerty-OFF, 2023-12-20:
Yes, we need an experiment.  Perhaps long-term operation with a current of 3 Amps will cause significant heating.  These outputs are unprotected.  Flyback diodes are present, you can control the inductive load using PWM.

ElDominio, 2023-12-20:
I don't think VVT solenoids ask for more than half an amp, so we should be fine?

rusefillc, 2023-12-20:
> we need an experiment

@ElDominio would you be able to make an experiment happen?

ElDominio, 2023-12-20:
What is the experiment

rusefillc, 2023-12-20:
@ElDominio please wire up a VVT solenoid on bench or real car and see what happens

ElDominio, 2024-02-23:
This will be tested eventually

ElDominio, 2024-05-16:
It may not be because #176 happened

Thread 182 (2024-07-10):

M54 wired as PNP has odd issues in cylinders 5 and 6

ElDominio, 2024-07-10:
Tune and log: https://rusefi.com/online/view.php?log=1411

The car fires injector and ignition 5 and 6, but unplugging them with engine running results in no change; the engine backfires sometimes, which is strange?
Coil 1 and 3 are swapped physically, so that's why the pins are swapped in firmware. Testing coils and injectors 1-6 is on the correct cylinders according to numbers on the Bench Test area.

It sounds as if 5 and 6 are firing in the wrong place, but they fire correctly in test mode? I am incredibly confused

rusefillc, 2024-07-12:
please remove fly back diodes?

please convert to batch fuel if above does not help?

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

rusefillc, 2024-07-12:
@ElDominio maybe those

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

rusefillc, 2024-07-12:
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

ElDominio, 2024-07-12:
Flyback diodes were the problem, removed and we have full power

rusefillc, 2024-07-12:
@ElDominio what's the next step for this ticket?

ElDominio, 2024-07-12:
Closing it? Remove it from default BOM?

rusefillc, 2024-07-12:
@ElDominio yes we can remove a couple of default BOM if you need

ElDominio, 2024-07-24:
removing diode was fix so i think it can be closed

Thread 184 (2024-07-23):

need boot times of under 350ms for car that expects fast CAN

ElDominio, 2024-07-23:
Mitsubishi lancer 2013+ expects ECU to wake up before power steering module, and in the current state 4chan takes too long. Any way to make this faster?

rusefillc, 2024-07-23:
@ElDominio fixed only for F7 boards

Closed 2024-07-23.

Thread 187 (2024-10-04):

Multiple 5V Supply issues

ElDominio, 2024-10-04:
I had had about 3-5 4chan from revisions E and older come back with dead 5V supply or strangely failing 5v supply.

Today's example: When the ECU is powered on after a long time of being powered off, anything powered by 5V will not work on first boot. If you power cycle the ECU, all 5v works fine.

To make sure of repeatability, I disconnected the ECU (from car and laptop), shorted 12v to GND (because I'm thinking some weird capacitor dark magic), plugged it back in. and when I booted it again 5V would be dead. Power cycling without disconnecting anything would fix the issue.

I have had a few other cases where 5V is dead and I only get about 1.37v and strange numbers like those, and I have no idea where to attack except replace (costly)

rusefillc, 2024-10-10:
@ElDominio how many of these can you ship to NJ?

I would love to help but it would require having problematic units locally

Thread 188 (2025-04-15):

SPI_SR_RXNE fatal error

ElDominio, 2025-04-15:
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

never have seen this error before? Somehow tune related, user assigned same pin to fan2 and ac_relay and this came up and never leaves

Will try restting to default tune then manually moving tune over

rusefillc, 2025-04-15:
we saw that before - so far assumption was always hardware issues, maybe shorted SD card? what else is SPI on 4chan?

https://github.com/rusefi/rusefi/issues/7351

ElDominio, 2025-04-15:
Related was SD card, I disabled SD card and unnassigned all SD pins and it came back to life

Closed 2025-04-29.

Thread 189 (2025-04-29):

Flex input not working for cam sensor

ElDominio, 2025-04-29:
Raymond wired cam sensor to flex input, there is no rising/falling VVT in this input. I searched schematic and saw

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

PA7/PE11? Which one is correct? Possible conflict? Flex can't be used as cam input?

rusefillc, 2025-04-29:
``
// fun fact: same input goes to TWO stm32 pins so that we can use it both as analog and ICU capture
``

step one: digital multimeter to confirm pull-up?

ElDominio, 2025-04-30:
pin reads 5v when powered through USB

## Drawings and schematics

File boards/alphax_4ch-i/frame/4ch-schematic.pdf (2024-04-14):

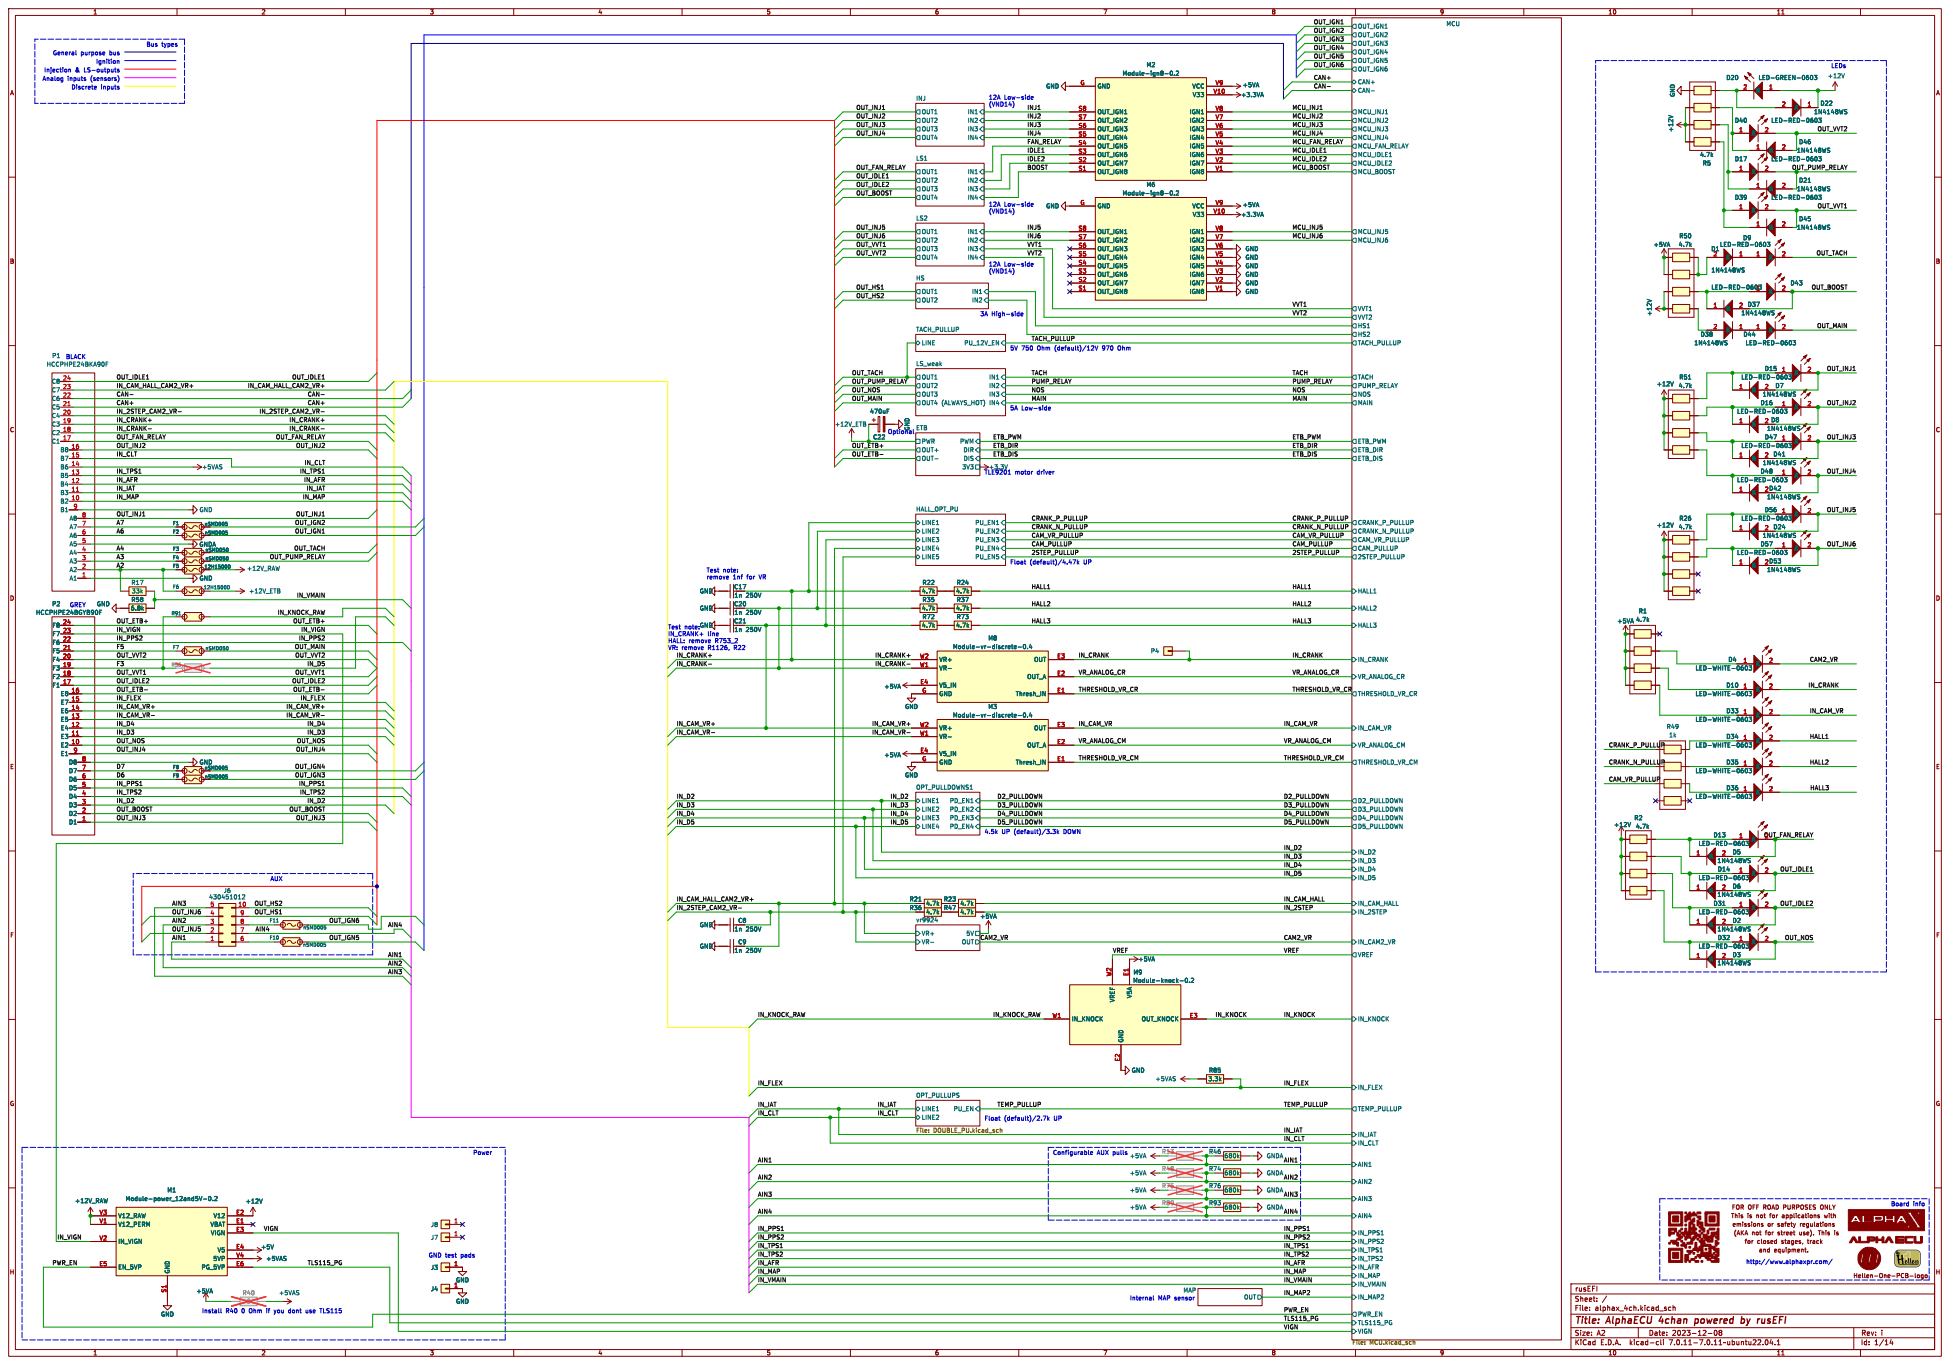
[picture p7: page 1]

+5VA GND GND GND GND GND GND

TLE9201 motor driver 5A Low-side

Test note: remove 1nf for VR

Test note:
IN_CRANK+ line HALL: remove R753_2 VR: remove R1126, R22

for closed stages, track FOR OFF ROAD PURPOSES ONLY

http://www.alphaxpr.com/

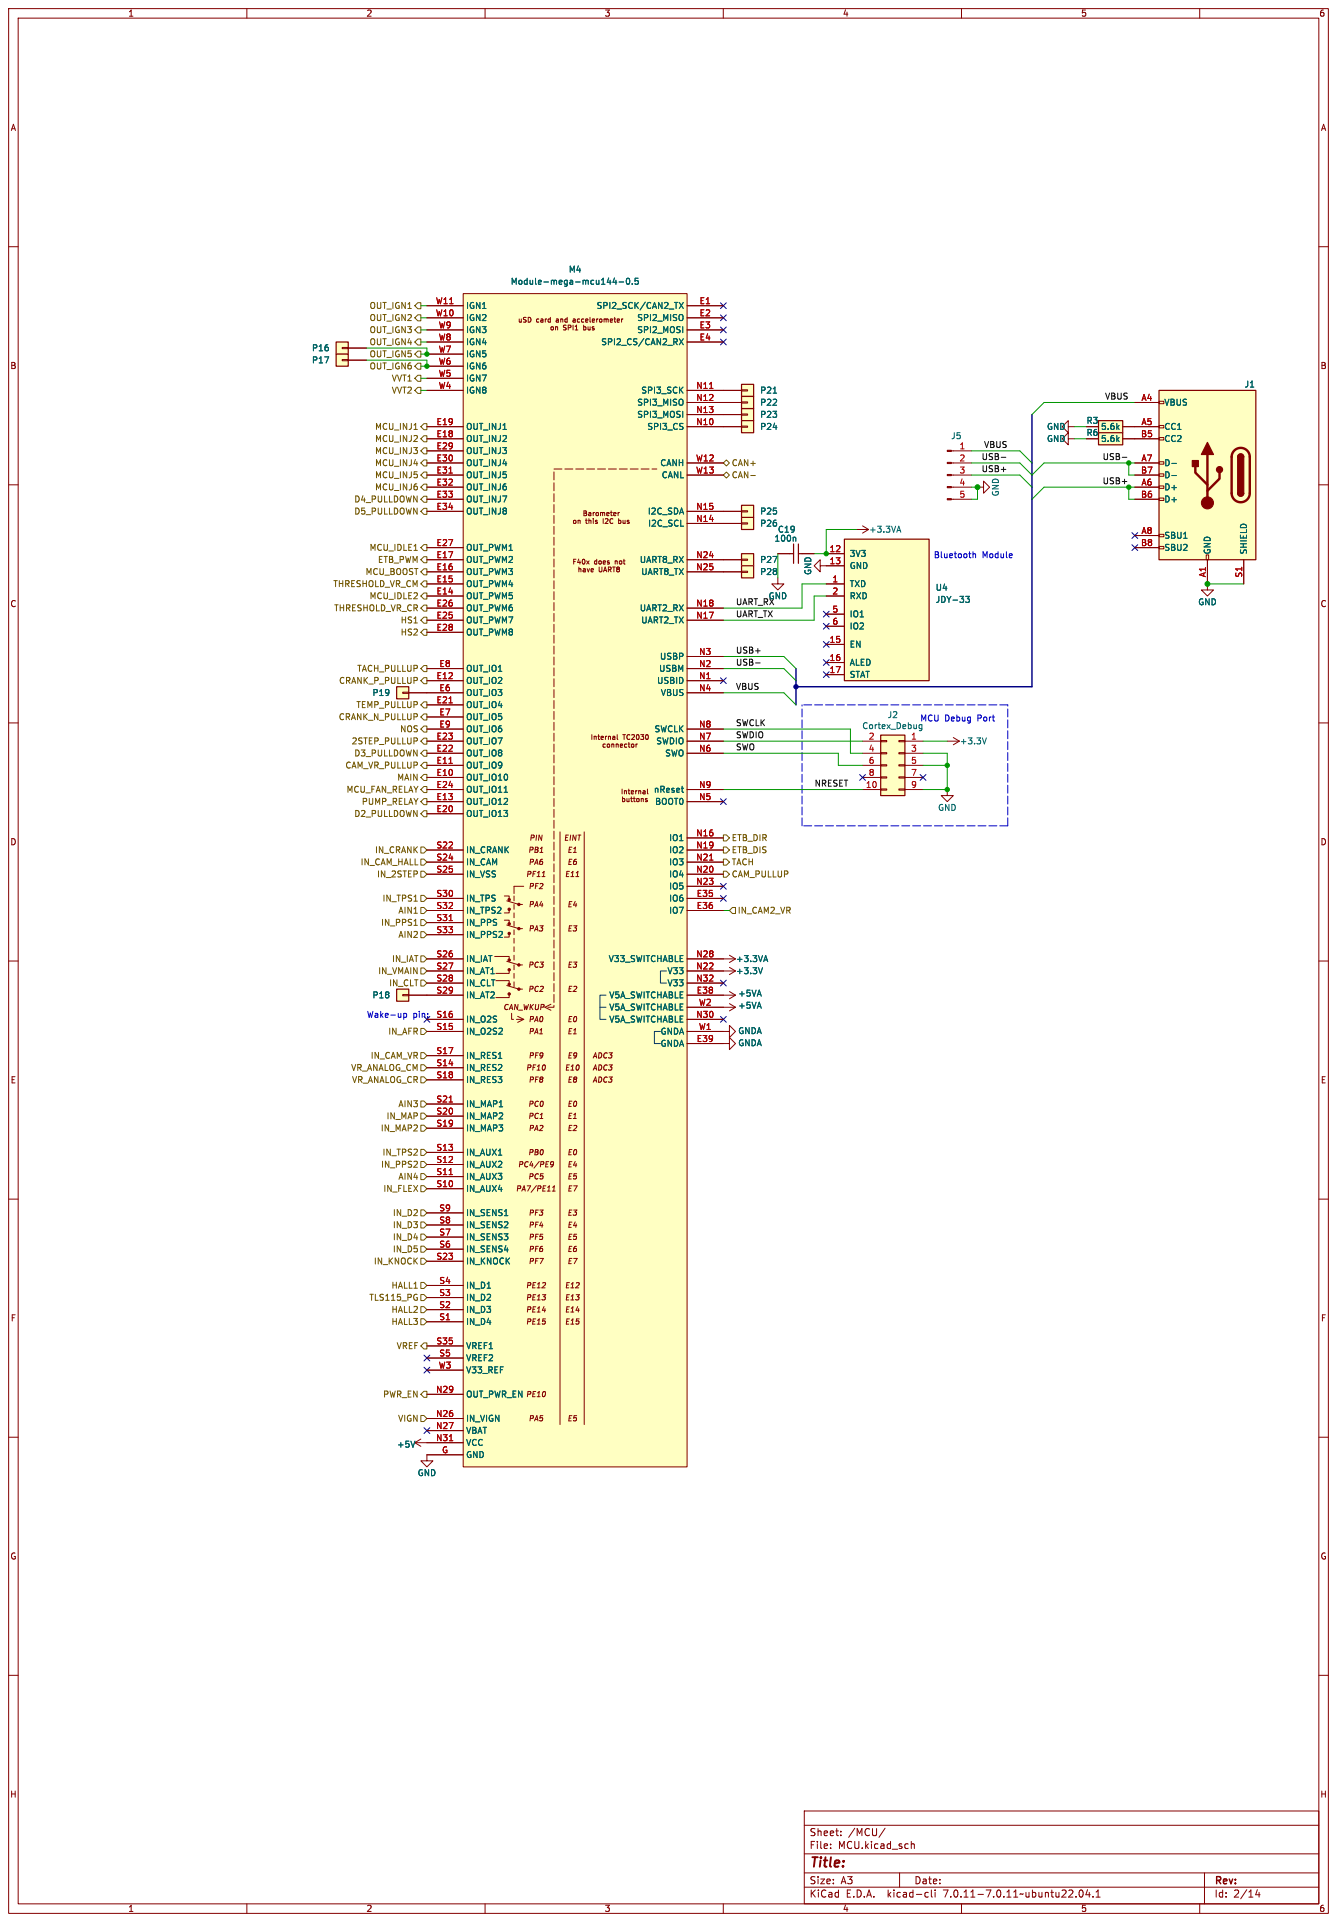
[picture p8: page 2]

3V3 12 GND 13 EN 15 ALED 16 STAT 17 RXD 2

Id: 2/14 Title: File: MCU.kicad_sch Sheet: /MCU/

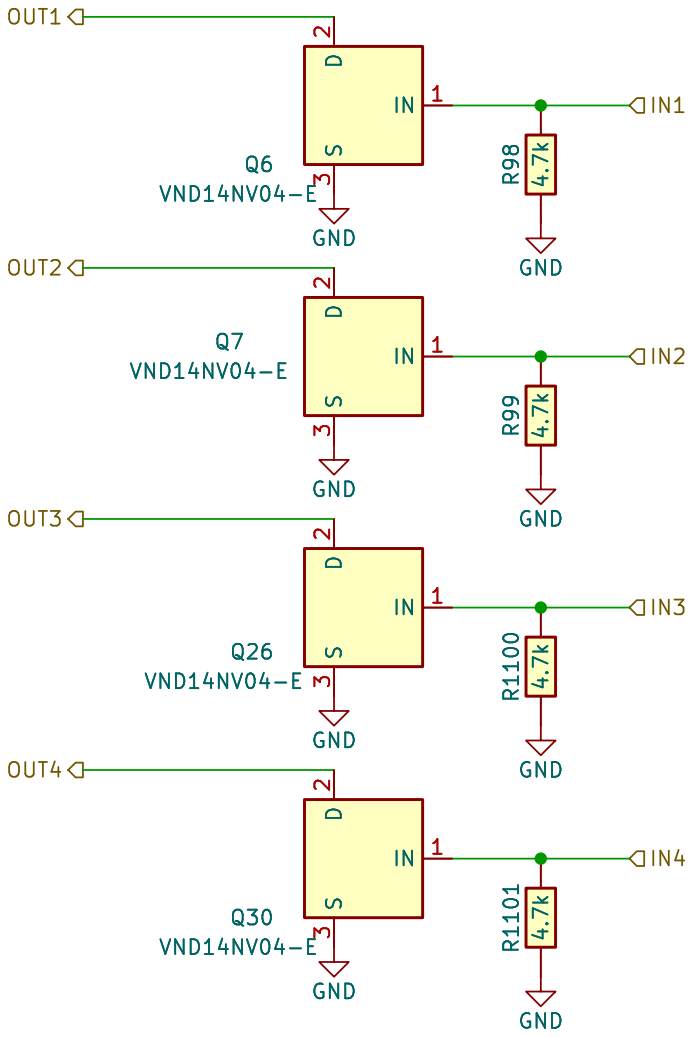
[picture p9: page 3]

3Q6 VND14NV04-E R1100 4.7k GND R99 4.7k GND GND GND

3 GND GND GND R99 4.7k GND R1100 4.7k

Id: 3/14 Title: File: INJ4.kicad_sch Sheet: /INJ/

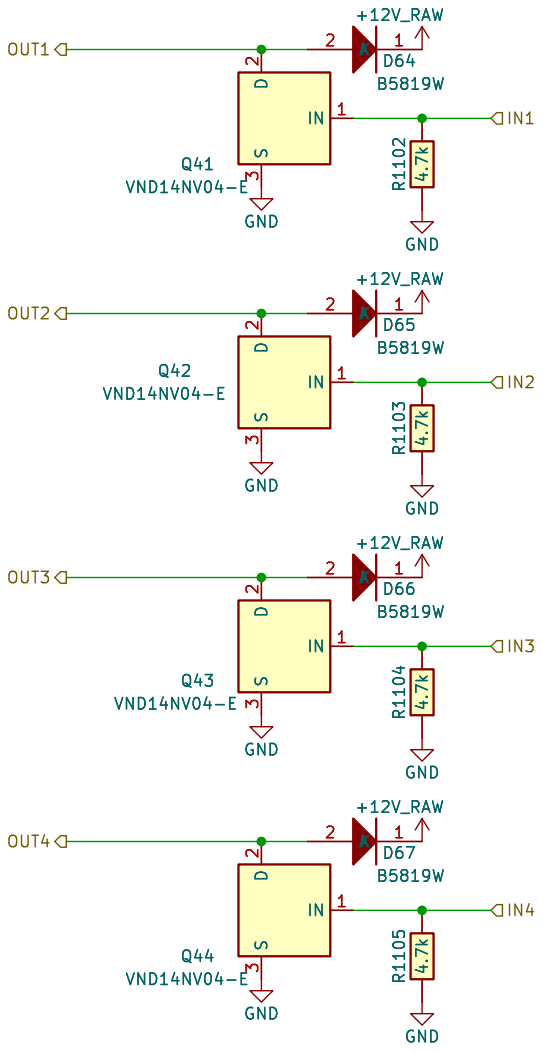
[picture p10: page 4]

Id: 4/14 Title: File: LS4.kicad_sch Sheet: /LS1/ GND

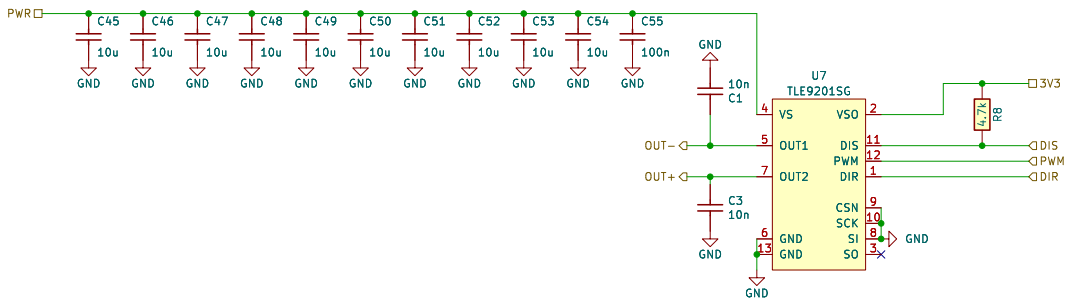
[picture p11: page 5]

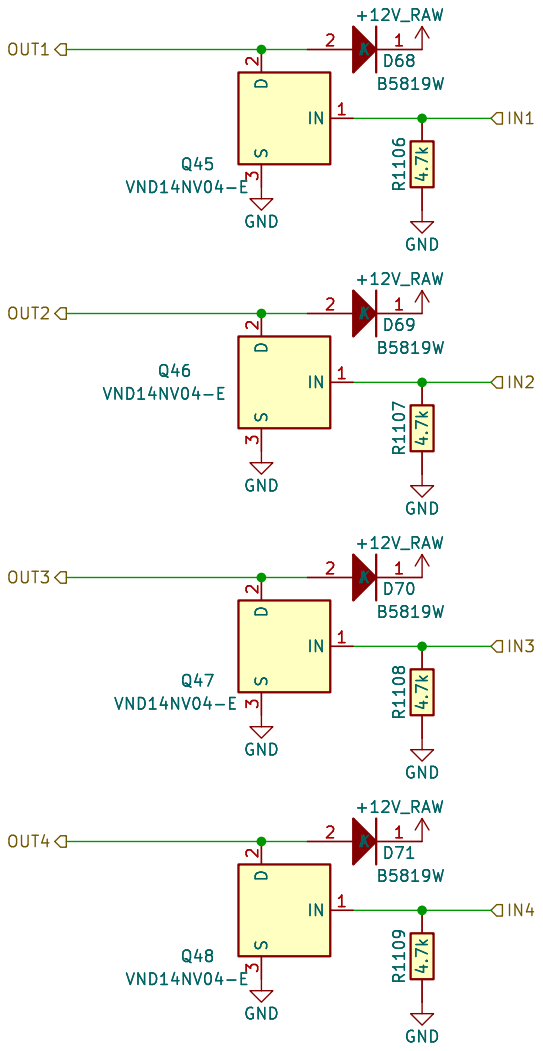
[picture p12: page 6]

Id: 6/14 Title: File: LS4.kicad_sch Sheet: /LS2/

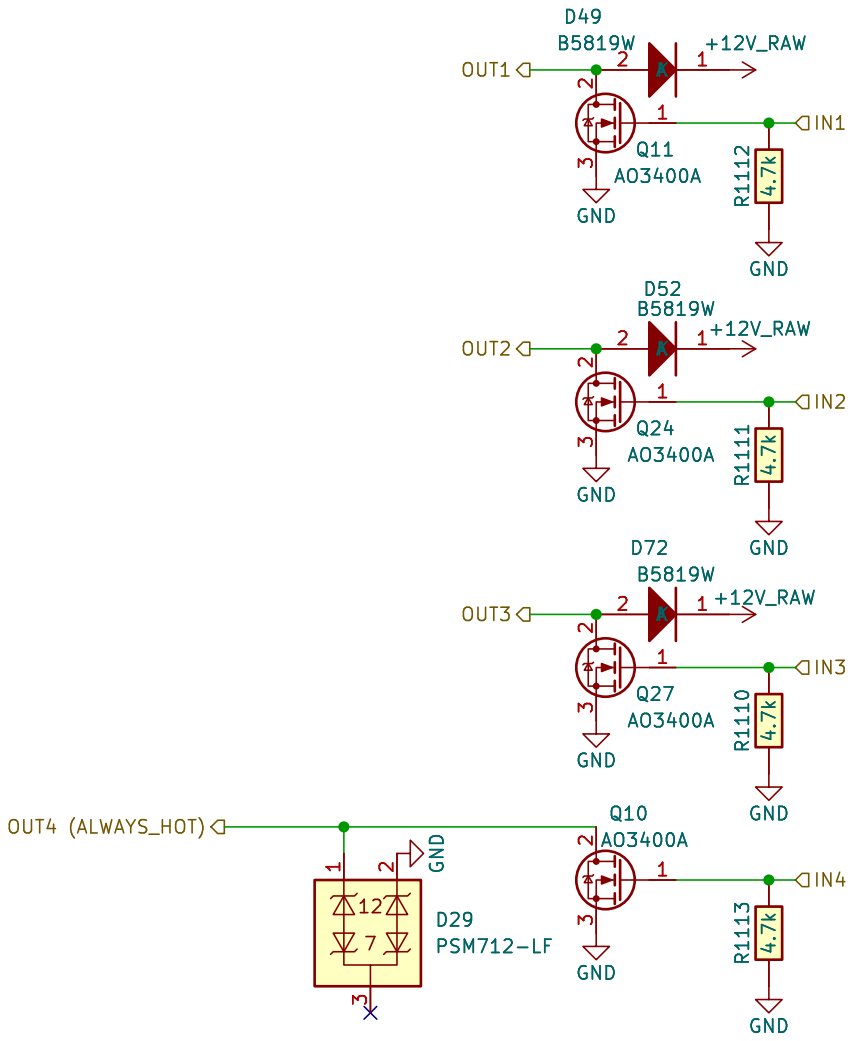
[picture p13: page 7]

Id: 7/14 Title: File: LS_weak.kicad_sch Sheet: /LS_weak/

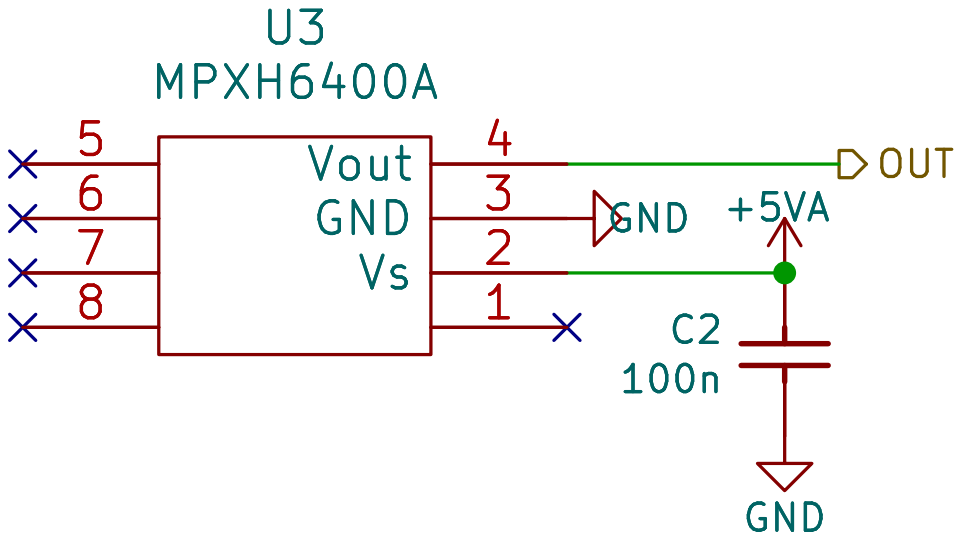
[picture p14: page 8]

Id: 8/14 Title: File: MAP.kicad_sch Sheet: /MAP/

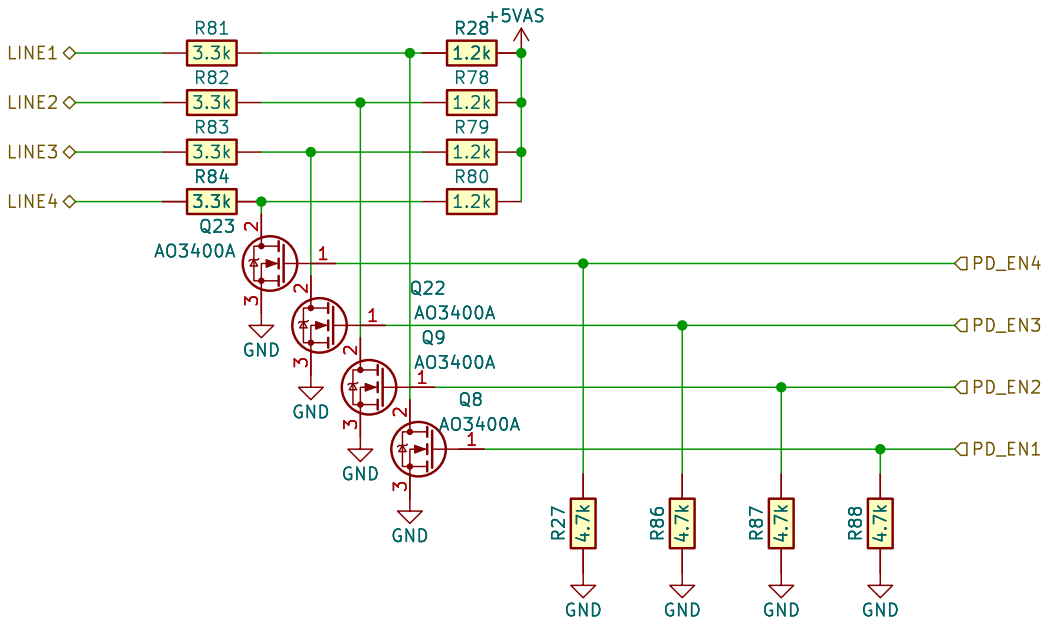
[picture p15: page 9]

2 3 GND GND R27 4.7k R86 4.7k GND GND GND R87 4.7k R88 4.7k R28

1.2k GND

Id: 9/14 Title: File: PD4.kicad_sch Sheet: /OPT_PULLDOWNS1/ GND

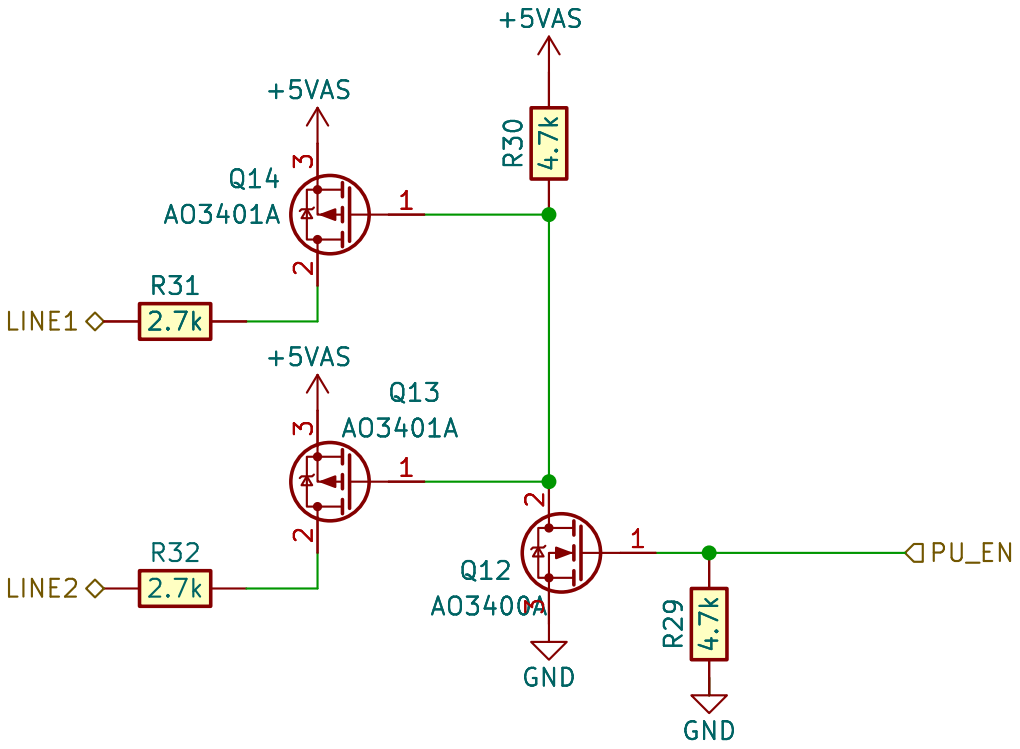
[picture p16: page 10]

Id: 11/14 Title: File: DOUBLE_PU.kicad_sch Sheet: /OPT_PULLUPS/

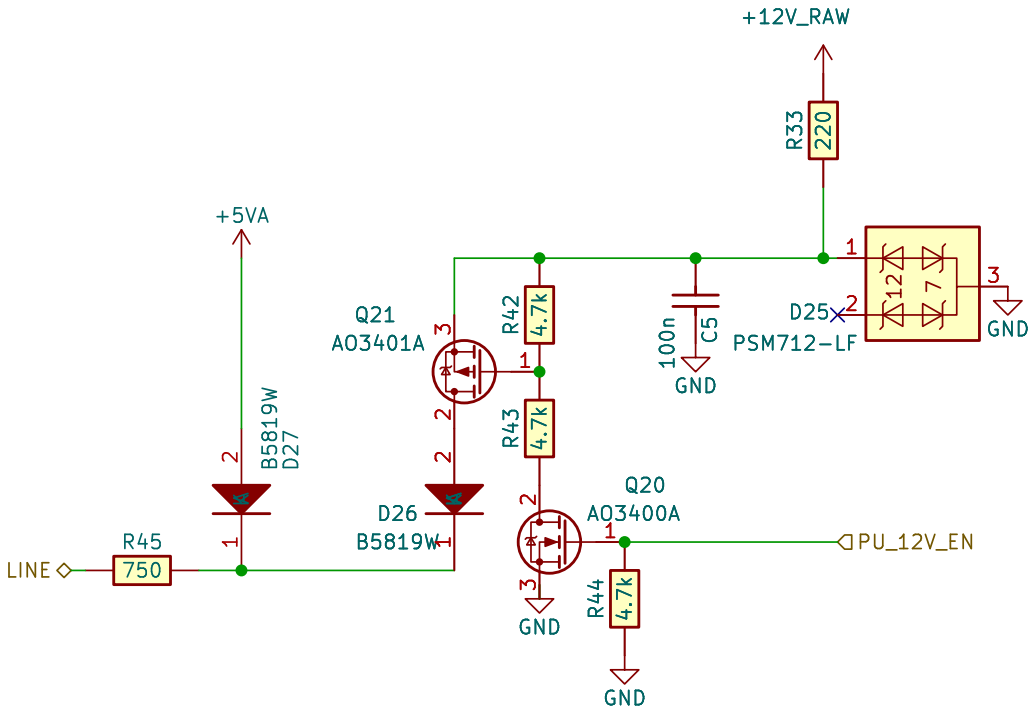
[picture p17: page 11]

Id: 12/14 Title: File: TACH_PU.kicad_sch Sheet: /TACH_PULLUP/

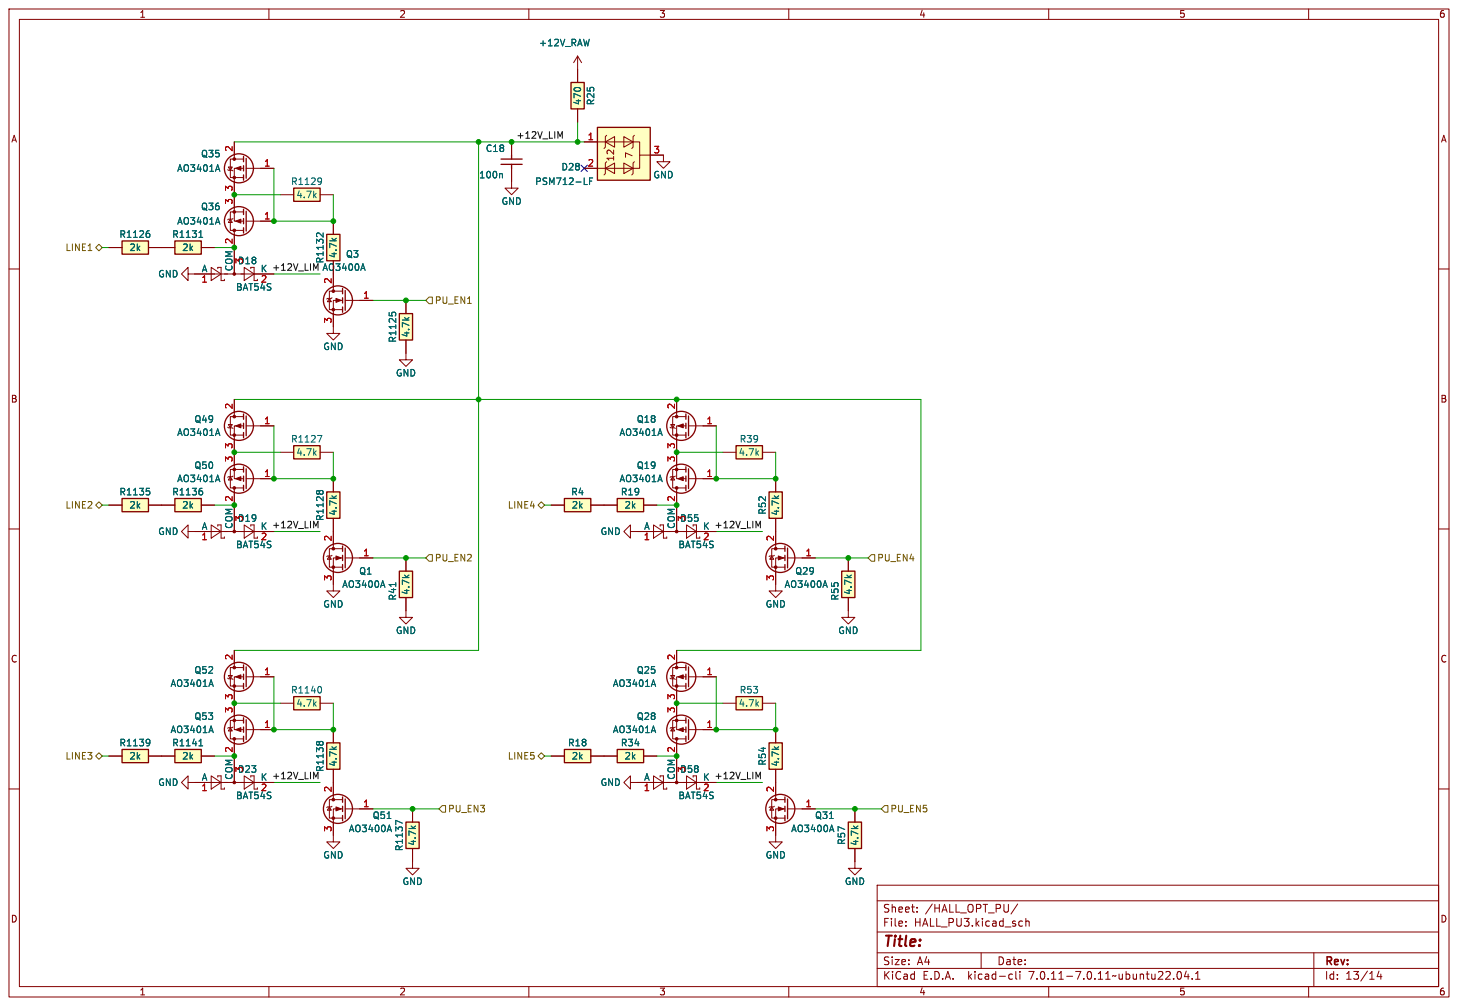
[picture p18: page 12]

Id: 13/14 Title: File: HALL_PU3.kicad_sch Sheet: /HALL_OPT_PU/ GND


Id: 14/14 Title: File: HS2.kicad_sch Sheet: /HS/


Id: 15/14 Title: File: vr9924.kicad_sch Sheet: /vr9924/

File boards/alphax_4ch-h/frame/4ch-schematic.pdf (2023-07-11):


Test note: remove 1nf for VR
IN_CRANK+ line HALL: remove R753_2 VR: remove R1126, R22 CAM HALL PU

R89 DNP R75 DNP R48 DNP R13 DNP

for closed stages, track FOR OFF ROAD PURPOSES ONLY

GND test pads * Warning! Remove R40 if you use TLS115

http://www.alphaxpr.com/

Id: 1/14 Title: AlphaECU 4chan powered by rusEFI File: alphax_4ch.kicad_sch Sheet: / rusEFI OUT MAP









2 3GND GND R27 4.7k R86 4.7k GND GND GND R87 4.7k GND R88 4.7k R28

2 3 Q8 AO3400A GND GND GND GND



Id: 12/14 Title: File: TACH_PU.kicad_sch Sheet: /TACH_PULLUP/




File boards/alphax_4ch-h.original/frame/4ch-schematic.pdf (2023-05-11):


Test note: remove 1nf for VR

Test note:
IN_CRANK+ line HALL: remove R753_2 VR: remove R1126, R22

Id: 1/14 Title: AlphaECU 4chan powered by rusEFI File: alphax_4ch.kicad_sch Sheet: / rusEFI LINE1

Power GND test pads

for closed stages, track FOR OFF ROAD PURPOSES ONLY

http://www.alphaxpr.com/


MCU Debug Port +5VA GNDA








2 3 GND GND R27 4.7k R86 4.7k GND GND GND R87 4.7k R88 4.7k R28

2 3 Q23 AO3400A R88 4.7k GND R27 4.7k R86 4.7k GND GND GND



Id: 12/14 Title: File: TACH_PU.kicad_sch Sheet: /TACH_PULLUP/




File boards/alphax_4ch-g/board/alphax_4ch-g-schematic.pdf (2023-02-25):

# 4.7k +5VA

# F40x does not have UART8 SPI1_SCK


Bluetooth Module Discrete inputs
Auxiliary bus

3 Q9 VND14NV04-E GND GND GND GND
2 Q22 VND14NV04-E

IAT N15 CLT N16 TPS N17 O2S N18 CAM N19 VSS N20 CRANK N21 KNOCK N22 SENS4 N23 SENS3 N24 SENS2 N25 SENS1 N26 RES2 N3 O2S2 N4 PPS N5 RES1 N6 AUX4 N7 AUX3 N8 AUX2 N9 M5AModule-input-0.1
IAT N15 CLT N16 TPS N17 O2S N18 CAM N19 VSS N20 CRANK N21 KNOCK N22 SENS4 N23 SENS3 N24 SENS2 N25 SENS1 N26 RES2 N3 O2S2 N4 PPS N5 RES1 N6 AUX4 N7 AUX3 N8 AUX2 N9

3 PG 5 ADJ 6 EN 8 GND +5V R3

2 3 GND GND GND GND

for closed stages, track FOR OFF ROAD PURPOSES ONLY
This is not for applications with
emissions or safety regulations
(AKA not for street use). This is

and equipment.
http://www.alphaxpr.com/

Id: 1/1 Title: AlphaECU 4chan powered by rusEFI

tfo rm m/s/h; Hellen-One Power1 2; dreik; Size:; Date:; Rev; Shee; VBA; GND S1; Hel; len O; wer-1; terface; VIGN; overvo; tect; 8 SMCJ; 1 PSM7; MIC5

rusEFI EMS https://rusefi.co
Hellen-One


## +5VGND

## +5VGND


Outputs a pulse on rising edge R751

Vref generation RS Latch Tracks which edge happened last
4 GND GND

Differential to single ended conversion

Outputs a pulse on falling edge

tfo rm m/s/h; Size; Dat; Rev; Shee; _IGN; VCC; DIR; LVC4

Hellen-One IGN8 andreika

rusEFI EMS https://rusefi.co
Hellen-One



D5 *D5 is digital-only on F429!(EINT11)

*A20-A23 are duplicated for ADC3
*VIGN input is unprotected!

PESD1CAN; GND; CANH; CANL; TXD 1 GND 2 VCC 3; Vio; 5 RXD 4; 6 CANH; TJA1051T/3/1J; CANH CANL; CAN_TX; CAN_RX; CAN_VIO; CAN_VIO V2; S2 CANL; CAN_TX V5; CAN_RX V6; Module:can/0.1

Hellen-One CAN


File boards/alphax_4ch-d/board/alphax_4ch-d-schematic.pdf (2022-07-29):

IGN8 | V1 V33 | V10

A1 1 B2 10 B3 11 B4 12 B5 13 B6 14 B7 15 B8 16 C1 17 C2 18 C3 19A2 2 C4 20 C5 21 C6 22 C7 23 C8 24A3 3 A4 4 A5 5 A6 6 A7 7 A8 8 B1 9 P1


+12V_RAW
IAT N15 CLT N16 TPS N17 O2S N18 CAM N19 VSS N20 CRANK N21 KNOCK N22 SENS4 N23 SENS3 N24 SENS2 N25 SENS1 N26 RES2 N3 O2S2 N4 PPS N5 RES1 N6 AUX4 N7 AUX3 N8 AUX2 N9 M5AModule-input-0.1

* Warning! Remove R40 is you use TLS115

3 PG 5 ADJ 6 EN 8 U1 TLS115 GND

for closed stages, track FOR OFF ROAD PURPOSES ONLY

File: alphax_4ch.kicad_sch Sheet: / rusEFI GND

emissions or safety regulations
(AKA not for street use). This is

and equipment.
http://www.alphaxpr.com/

Id: 1/1 Title: AlphaECU 4chan powered by rusEFI

tfo rm m/s/h; Hellen-One Power1 2; dreik; Size:; Date:; Rev; Shee; VBA; GND S1; Hel; len O; wer-1; terface; VIGN; overvo; tect; 8 SMCJ; 1 PSM7; MIC5

rusEFI EMS https://rusefi.co
Hellen-One


# +5V GND


Outputs a pulse on falling edge

tfo rm m/s/h; Size; Dat; Rev; Shee; _IGN; VCC; DIR; LVC4

Hellen-One IGN8 andreika

rusEFI EMS https://rusefi.co
Hellen-One



D5 *D5 is digital-only on F429!(EINT11)

*A20-A23 are duplicated for ADC3
*VIGN input is unprotected!

PESD1CAN; GND; CANH; CANL; TXD 1 GND 2 VCC 3; Vio; 5 RXD 4; 6 CANH; TJA1051T/3/1J; CANH CANL; CAN_TX; CAN_RX; CAN_VIO; CAN_VIO V2; S2 CANL; CAN_TX V5; CAN_RX V6; Module:can/0.1

Hellen-One CAN


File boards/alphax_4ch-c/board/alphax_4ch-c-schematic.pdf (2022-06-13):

A1 1 B2 10 B3 11 B4 12 B5 13 B6 14 B7 15 B8 16 C1 17 C2 18 C3 19A2 2 C4 20 C5 21 C6 22 C7 23 C8 24A3 3 A4 4 A5 5 A6 6 A7 7 A8 8 B1 9 P1

IGN8 | V1 V33 | V10


* Warning! Remove R40 is you use TLS115

for closed stages, track FOR OFF ROAD PURPOSES ONLY
This is not for applications with
emissions or safety regulations
(AKA not for street use). This is

and equipment.
http://www.alphaxpr.com/

Id: 1/1 Title: AlphaECU 4chan powered by rusEFI

tfo rm m/s/h; Hellen-One Power1 2; dreik; Size:; Date:; Rev; Shee; VBA; GND S1; Hel; len O; wer-1; terface; VIGN; overvo; tect; 8 SMCJ; 1 PSM7; MIC5

rusEFI EMS https://rusefi.co
Hellen-One


# +5V GND


Outputs a pulse on falling edge

tfo rm m/s/h; Size; Dat; Rev; Shee; _IGN; VCC; DIR; LVC4

Hellen-One IGN8 andreika

rusEFI EMS https://rusefi.co
Hellen-One



D5 *D5 is digital-only on F429!(EINT11)

*A20-A23 are duplicated for ADC3
*VIGN input is unprotected!

PESD1CAN; GND; CANH; CANL; TXD 1 GND 2 VCC 3; Vio; 5 RXD 4; 6 CANH; TJA1051T/3/1J; CANH CANL; CAN_TX; CAN_RX; CAN_VIO; CAN_VIO V2; S2 CANL; CAN_TX V5; CAN_RX V6; Module:can/0.1

Hellen-One CAN


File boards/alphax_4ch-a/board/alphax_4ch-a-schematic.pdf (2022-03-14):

IGN8 | V1 V33 | V10

A1 1 B2 10 B3 11 B4 12 B5 13 B6 14 B7 15 B8 16 C1 17 C2 18 C3 19A2 2 C4 20 C5 21 C6 22 C7 23 C8 24A3 3 A4 4 A5 5 A6 6 A7 7 A8 8 B1 9 P1


3 D49 PSM712 GND GND GND GND

IAT N15 CLT N16 TPS N17 O2S N18 CAM N19 VSS N20 CRANK N21 KNOCK N22 SENS4 N23 SENS3 N24 SENS2 N25 SENS1 N26 RES2 N3 O2S2 N4 PPS N5 RES1 N6 AUX4 N7 AUX3 N8 AUX2 N9 M5AModule-input-0.1

* Warning! Remove R40 is you use TLS115
4.7k +5VAS GND

for closed stages, track FOR OFF ROAD PURPOSES ONLY
This is not for applications with
emissions or safety regulations
(AKA not for street use). This is

and equipment.
http://www.alphaxpr.com/

Id: 1/1 Title: AlphaECU 4chan powered by rusEFI

tfo rm m/s/h; Hellen-One Power1 2; dreik; Size:; Date:; Rev; Shee; VBA; GND S1; Hel; len O; wer-1; terface; VIGN; overvo; tect; 8 SMCJ; 1 PSM7; MIC5

rusEFI EMS https://rusefi.co
Hellen-One


# +5V GND


Outputs a pulse on falling edge

tfo rm m/s/h; Size:; Rev; Shee; VCC; APW

Hellen-One IGN8 andreika

rusEFI EMS https://rusefi.co
Hellen-One



D5 *D5 is digital-only on F429!(EINT11)

*A20-A23 are duplicated for ADC3
*VIGN input is unprotected!

PESD1CAN; GND; CANH; CANL; TXD 1 GND 2 VCC 3; Vio; 5 RXD 4; 6 CANH; TJA1051T/3/1J; CANH CANL; CAN_TX; CAN_RX; CAN_VIO; CAN_VIO V2; S2 CANL; CAN_TX V5; CAN_RX V6; Module:can/0.1

Hellen-One CAN

https://rusefi.com/s/hellen72

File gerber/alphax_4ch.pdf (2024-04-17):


+5VA GND GND GND GND GND GND

TLE9201 motor driver 5A Low-side

Test note: remove 1nf for VR

Test note:
IN_CRANK+ line HALL: remove R753_2 VR: remove R1126, R22

for closed stages, track FOR OFF ROAD PURPOSES ONLY

http://www.alphaxpr.com/


100n P28GND
3V3 12 GND 13 EN 15 ALED 16 STAT 17 RXD 2
IO2 6 GND
JDY-33 TXD 1

Id: 2/14 Title: File: MCU.kicad_sch Sheet: /MCU/


Id: 3/14 Title: File: INJ4.kicad_sch Sheet: /INJ/


Id: 4/14 Title: File: LS4.kicad_sch Sheet: /LS1/ GND



Id: 6/14 Title: File: LS4.kicad_sch Sheet: /LS2/



Id: 8/14 Title: File: MAP.kicad_sch Sheet: /MAP/


2 3 GND GND R27 4.7k R86 4.7k GND GND GND R87 4.7k R88 4.7k R28

1.2k GND

Id: 9/14 Title: File: PD4.kicad_sch Sheet: /OPT_PULLDOWNS1/ GND


Id: 11/14 Title: File: DOUBLE_PU.kicad_sch Sheet: /OPT_PULLUPS/


Id: 12/14 Title: File: TACH_PU.kicad_sch Sheet: /TACH_PULLUP/



Id: 14/14 Title: File: HS2.kicad_sch Sheet: /HS/


Id: 15/14 Title: File: vr9924.kicad_sch Sheet: /vr9924/

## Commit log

2022-03-04 first draft schematics
    [alphax_4ch.kicad_sch, board_id_alpha4ch-a.csv, bom_replace_alphax-4ch-a.csv]
2022-03-11 tiny update
    [alphax_4ch.kicad_sch]
2022-03-12 update schem
    [alphax_4ch.kicad_sch]
2022-03-14 rev.A schematics & pcb files
    [alphax_4ch-B_Cu.gbl, alphax_4ch-B_Fab.gbr, alphax_4ch-B_Mask.gbs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]
2022-03-15 jlc bom replacements
    [alphax_4ch-a-BOM.csv, bom_replace_alphax-4ch-a.csv]
2022-03-15 fix fuses
    [alphax_4ch-a-BOM.csv, bom_replace_alphax-4ch-a.csv]
2022-03-15 fab files 2022-03-15
    [alphax_4ch-a-BOM.2022-03-15.csv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]
2022-03-31 https://github.com/rusefi/alphax-4chan/issues/10 https://github.com/rusefi/alphax-4chan/issues/9 https://github.com/rusefi/alphax-4chan/issues/12
    [alphax_4ch.kicad_sch]
2022-04-27 rev.B gerbers
    [4ch-BOM.csv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]
2022-05-22 trying new convention
    [bom_replace_alphax-4ch-с-wip.csv]
2022-05-22 huh that was fun
    [bom_replace_alphax_4ch-c-wip.csv]
2022-05-22 Auto-generated board
    [4ch-BOM.csv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]
2022-06-10 rev.C release candidate
    [alphax_4ch-B_Cu.gbl, alphax_4ch-B_Fab.gbr, alphax_4ch-B_Mask.gbs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]
2022-06-11 rev.C BOM replacements
    [4ch-BOM.csv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]
2022-06-11 more beefy vias
    [alphax_4ch-B_Cu.gbl, alphax_4ch-B_Fab.gbr, alphax_4ch-B_Mask.gbs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]
2022-07-21 non-jlc BOM
    [alphax_4ch-c-BOM.non-jlc.csv]
2022-07-23 rev.D draft
    [alphax_4ch-B_Cu.gbl, alphax_4ch-B_Fab.gbr, alphax_4ch-B_Mask.gbs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]
2022-07-23 [skip actions] Auto-generated board
    [4ch-BOM.csv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]
2022-07-25 rev.D https://github.com/rusefi/alphax-4chan/issues/45 https://github.com/rusefi/alphax-4chan/issues/46 https://github.com/rusefi/alphax-4chan/issues/47
    [4ch-BOM.csv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]
2022-07-29 rev.D: https://github.com/rusefi/alphax-4chan/issues/43 https://github.com/rusefi/alphax-4chan/issues/49
    [alphax_4ch-B_Cu.gbl, alphax_4ch-B_Fab.gbr, alphax_4ch-B_Mask.gbs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]
2022-08-01 no TLE9201SG - U6,"IFX9201SG","Infineon_PG-DSO-12-11","C112633"
    [bom_replace_alphax_4ch-d.csv]
2022-08-21 rev.E draft + sd-card fix (#59)
    [alphax_4ch-B_Cu.gbl, alphax_4ch-B_Fab.gbr, alphax_4ch-B_Mask.gbs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]
2022-08-21 no longer WIP
    [bom_replace_alphax_4ch-e.csv]
2022-08-22 E is ready
    [4ch-BOM.csv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]
2022-10-18 fab 220905
    [4ch-BOM.csv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]
2022-11-06 just a copy
    [alphax_4ch-e-BOM.20221106.csv]
2022-11-06 Let's use VND10N06TR-E #70
    [alphax_4ch-e-BOM.20221106.csv]
2022-11-06 parts shortage today #71
    [alphax_4ch-e-BOM.20221106.csv]
2023-01-29 New revision: silk and board ID rev F #86
    [board_id_alpha4ch-a.csv, board_id_alpha4ch-b.csv, board_id_alpha4ch-c.csv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]
2023-01-31 fresh about PDF case
2023-01-31 JLS parts #93
    [bom_replace_alphax_4ch-f.csv]
2023-02-02 JLS parts fix #93
    [bom_replace_alphax_4ch-f.csv]
2023-02-02 Upd PCB
    [alphax_4ch-B_Cu.gbl, alphax_4ch-B_Fab.gbr, alphax_4ch-B_Mask.gbs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]
2023-02-03 rev F
    [4ch-BOM.csv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]
2023-02-03 100k fix
    [alphax_4ch-f-BOM.csv]
2023-02-07 add bom_replace_alphax_4ch-g.csv
    [bom_replace_alphax_4ch-g.csv]
2023-02-25 Upd SCH
    [alphax_4ch.kicad_sch]
2023-02-27 no software for accelerometer
    [bom_replace_alphax_4ch-g.csv]
2023-03-31 rev F shortage today #116 SD J9
    [alphax_4ch-f-BOM.20230331.csv]
2023-03-31 rev F shortage today #116 any SMCJ30A he said
    [alphax_4ch-f-BOM.20230331.csv]
2023-04-01 Lua takes RAM let's go F42x
    [alphax_4ch-f-BOM.20230331.csv, bom_replace_alphax_4ch-g.csv]
2023-04-02 Fab preview
    [LS_weak.kicad_sch, MCU.kicad_sch, TACH_PU.kicad_sch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]
2023-04-02 10k fix
    [ETB.kicad_sch, alphax_4ch.csv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]
2023-04-02 Duplicate designators fix
    [HALL_PU3.kicad_sch, INJ4.kicad_sch, LS4.kicad_sch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]
2023-04-02 Upd replace
    [bom_replace_alphax_4ch-g.csv]
2023-04-04 4chan now prefers F42x for extra RAM (we have embedded Lua interpreter some scripts take RAM)
    [alphax_4ch-g-BOM.csv, bom_replace_alphax_4ch-g.csv]
2023-05-11 Fab export
    [MCU.kicad_sch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]
2023-05-11 VR caps, AUX conn symbol, HALL pullups resistors
    [alphax_4ch-B_Cu.gbl, alphax_4ch-B_Fab.gbr, alphax_4ch-B_Mask.gbs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]
2023-05-11 Fix pullups.csv link
    [bom_replace_alphax_4ch-h.csv]
2023-05-18 PN fixes
    [HALL_PU3.kicad_sch, alphax_4ch.kicad_sch, bom_pullups_alphax_4ch-i.csv]
2023-06-15 exact copy
    [alphax_4ch-h-BOM-JLC-F7.csv]
2023-07-10 preserving as is
    [4ch-BOM.csv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]
2023-07-11 Rev H*: #140, #142, #144, #145
    [HALL_PU3.kicad_sch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]
2023-12-09 PSM712-LF value fix
    [LS_weak.kicad_sch]
2023-12-10 3D pcb with main connector and USB #170
2023-12-11 [skip actions] Auto-generated board v2.1
    [alphax_4ch-B_Cu.gbl, alphax_4ch-B_Mask.gbs, alphax_4ch-B_Paste.gbp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]
2023-12-16 Main relay voltage AT1
    [MCU.kicad_sch, alphax_4ch.kicad_sch, bom_pullups_alphax_4ch-i.csv]
2023-12-21 # F7 is even better than F42x! U105,"STM32F767","LQFP144","C91685"
    [bom_replace_alphax_4ch-i.csv]
2023-12-22 P1 is available
    [bom_replace_alphax_4ch-i.csv]
2023-12-22 Blue LEDs
    [bom_replace_alphax_4ch-i.csv]
2023-12-22 Green LEDs
    [bom_replace_alphax_4ch-i.csv]
2024-04-05 with MAP sensor
    [bom_replace_alphax_4ch-i.csv]
2024-04-14 fab rev i #177
    [bom_replace_alphax_4ch-i.csv]
